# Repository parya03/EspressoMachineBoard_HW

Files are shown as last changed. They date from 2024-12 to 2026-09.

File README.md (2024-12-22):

Espresso Machine Board Project
Make a new controller for my Chefman CraftBrew

TODO Documentation

Power converter KiCad symbol and footprint from:
https://github.com/yaserharba/WX-DC12003_Kicad

Reverse Engineering notes for now:

Single shot brew temp: ~180 F
Steam temp: ~205 F at valve, ~230F at boiler
NTC 100k(?) Thermistor
- ~114kOhm at ~22.5C
CMS79FT738 MCU
13 x 6 cm board
3/16” OD, 1/8”(?) ID tubing

Why is OPV before boiler? Where to put actual pressure sensor?

Label says 1350W power consumption, 120VAC 60Hz

Board mounting screw:
30-23.5‎ = 6.5 from edge of hole to edge of hole
Right side hole positioned at 3.5cm from top, 2.5mm from right side of board (to middle of hole)

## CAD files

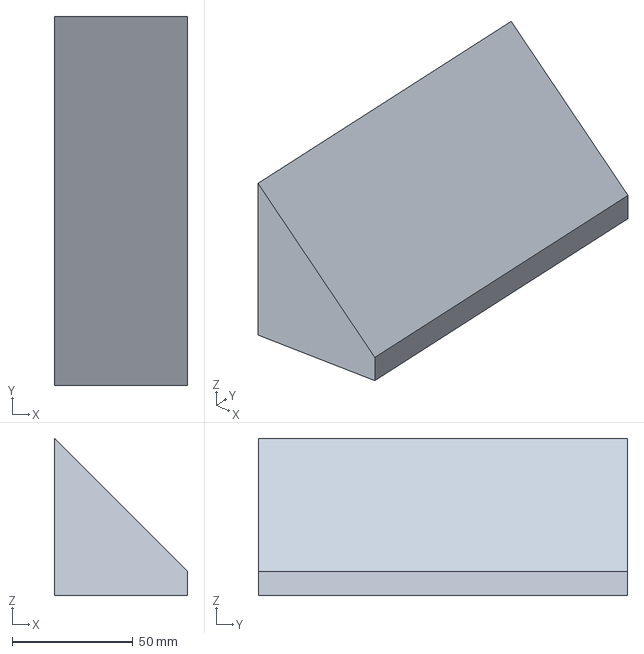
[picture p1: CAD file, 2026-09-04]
3DPrint/EspressoMachineBoardEnclosure.FCStd
55.2 x 153.0 x 65.2 mm

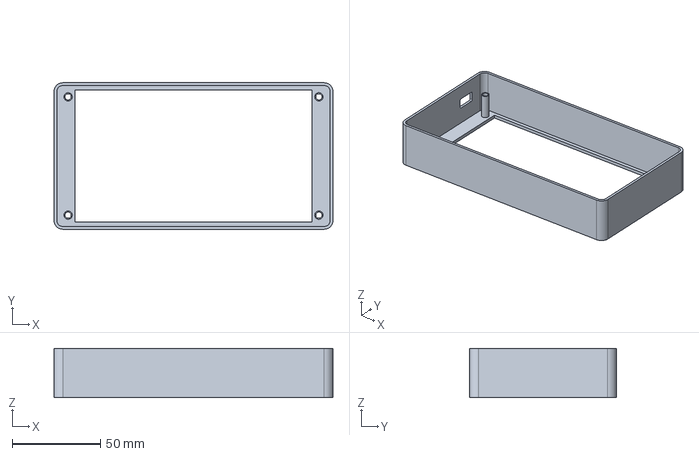
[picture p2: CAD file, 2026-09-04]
3DPrintSmall/CoffeeMachineSmallEnclosure.FCStd
158.0 x 83.0 x 28.0 mm

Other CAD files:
3DPrintSmall/CoffeeMachineSmallEnclosure-Body.3mf

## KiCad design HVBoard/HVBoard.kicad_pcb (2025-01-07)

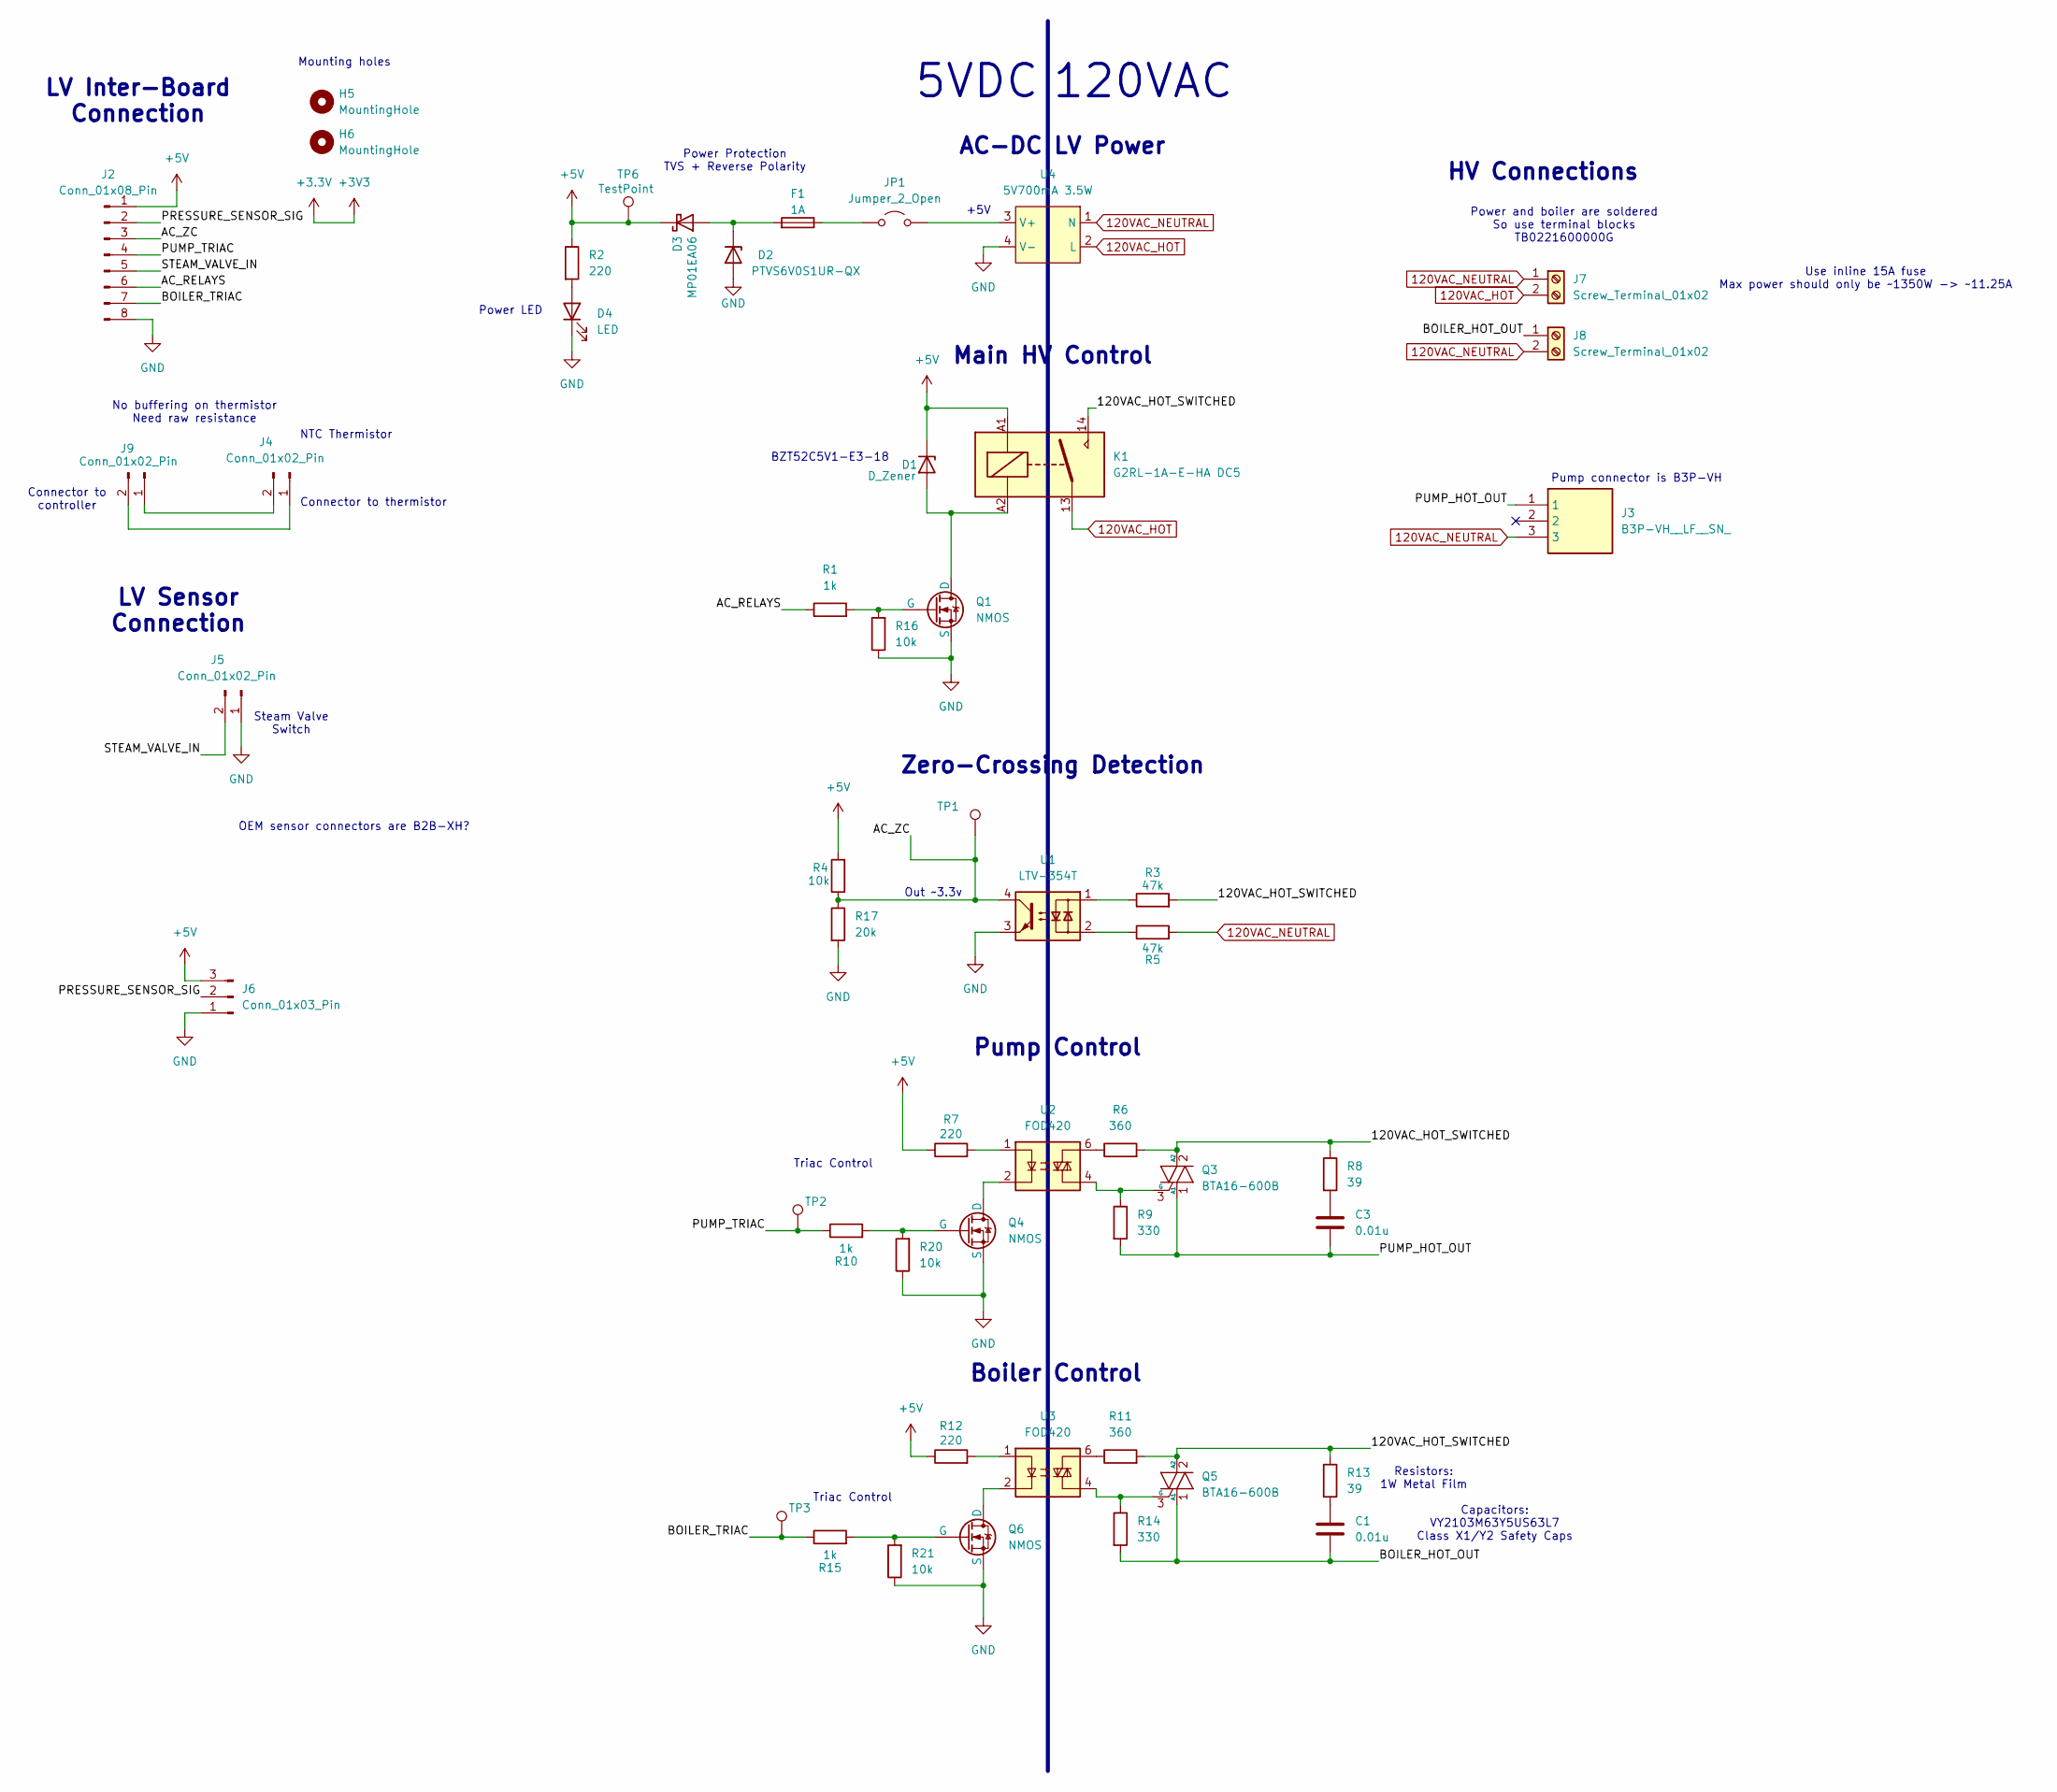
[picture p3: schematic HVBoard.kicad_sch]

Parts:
C1, C3: 0.01u; C_Disc_D11.0mm_W5.0mm_P7.50mm
D1: D_Zener; D_SOD-123
D2: PTVS6V0S1UR-QX; Nexperia_CFP3_SOD-123W
D3: MP01EA06; D_SOD-123
D4: LED; LED_0603_1608Metric; Mouser # 755-SMLD12EN1WT86
F1: 1A; Fuse_0603_1608Metric_Pad1.05x0.95mm_HandSolder
H5, H6: MountingHole; MountingHole_3.2mm_M3
J2: Conn_01x08_Pin; JST_PH_B8B-PH-K_1x08_P2.00mm_Vertical
J3: B3P-VH__LF__SN_; HDRV3W114P0X396_1X3_1182X850X1090P; Manufacturer_Part_Number B3P-VH (LF)(SN)
J4, J5, J9: Conn_01x02_Pin; JST_XH_B2B-XH-AM_1x02_P2.50mm_Vertical
J6: Conn_01x03_Pin; JST_XH_B3B-XH-AM_1x03_P2.50mm_Vertical
J7, J8: Screw_Terminal_01x02; TerminalBlock_bornier-2_P5.08mm
JP1: Jumper_2_Open; SolderJumper-2_P1.3mm_Open_Pad1.0x1.5mm
K1: G2RL-1A-E-HA DC5; Relay_SPST_Omron_G2RL-1A-E
Q1, Q4, Q6: NMOS; SOT-23
Q3, Q5: BTA16-600B; TO-220-3_Vertical
R1, R10, R15: 1k; R_0603_1608Metric_Pad0.98x0.95mm_HandSolder
R2: 220; R_0603_1608Metric; Mouser # 71-CRCW0603-665-E3
R3, R5: 47k; R_1206_3216Metric_Pad1.30x1.75mm_HandSolder
R4, R16, R20, R21: 10k; R_0603_1608Metric_Pad0.98x0.95mm_HandSolder
R6, R11: 360; R_1206_3216Metric_Pad1.30x1.75mm_HandSolder
R7, R12: 220; R_0603_1608Metric_Pad0.98x0.95mm_HandSolder
R8, R13: 39; R_Axial_DIN0207_L6.3mm_D2.5mm_P10.16mm_Horizontal
R9, R14: 330; R_1206_3216Metric_Pad1.30x1.75mm_HandSolder
R17: 20k; R_0603_1608Metric_Pad0.98x0.95mm_HandSolder
TP1, TP2, TP3, TP6: TestPoint; PinHeader_1x01_P2.54mm_Vertical
U1: LTV-354T; SO-4_4.4x3.6mm_P2.54mm
U2, U3: FOD420; DIP-6_W7.62mm
U4: 5V700mA 3.5W; WX-DC12003

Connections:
120VAC_HOT: J7.2, K1.13, U4.2 (L)
120VAC_NEUTRAL: J3.3, J7.1, J8.2, R5.2, U4.1 (N)
+5V: D1.1 (K), D3.1 (K), J2.1, J6.3, K1.A1, R2.1, R4.2, R7.1, R12.1, TP6.1
/120VAC_HOT_SWITCHED: K1.14, Q3.2 (A2), Q5.2 (A2), R3.2, R6.2, R8.1, R11.2, R13.1
/AC_RELAYS: J2.6, R1.1
/AC_ZC: J2.3, R4.1, R17.1, TP1.1, U1.4
/BOILER_HOT_OUT: C1.2, J8.1, Q5.1 (A1), R14.2
/BOILER_TRIAC: J2.7, R15.1, TP3.1
/PRESSURE_SENSOR_SIG: J2.2, J6.2
/PUMP_HOT_OUT: C3.2, J3.1, Q3.1 (A1), R9.2
/PUMP_TRIAC: J2.4, R10.1, TP2.1
/STEAM_VALVE_IN: J2.5, J5.2
GND: D2.2 (A), D4.1 (K), J2.8, J5.1, J6.1, Q1.3 (S), Q4.3 (S), Q6.3 (S), R16.1, R17.2, R20.1, R21.1, U1.3, U4.4 (V-)
unnamed: C1.1, R13.2
unnamed: C3.1, R8.2
unnamed: D1.2 (A), K1.A2, Q1.1 (D)
unnamed: D2.1 (K), D3.2 (A), F1.2
unnamed: D4.2 (A), R2.2
unnamed: J4.1, J9.2
unnamed: J4.2, J9.1
unnamed: JP1.1 (A), U4.3 (V+)
unnamed: F1.1, JP1.2 (B)
unnamed: Q1.2 (G), R1.2, R16.2
unnamed: Q3.3 (G), R9.1, U2.4
unnamed: Q4.1 (D), U2.2
unnamed: Q4.2 (G), R10.2, R20.2
unnamed: Q5.3 (G), R14.1, U3.4
unnamed: Q6.1 (D), U3.2
unnamed: Q6.2 (G), R15.2, R21.2
unnamed: R3.1, U1.1
unnamed: R5.1, U1.2
unnamed: R6.1, U2.6
unnamed: R7.2, U2.1
unnamed: R11.1, U3.6
unnamed: R12.2, U3.1

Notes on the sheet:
Connector to thermistor
Zero-Crossing Detection
Triac Control
Connector to controller
Mounting holes
Power and boiler are soldered So use terminal blocks TB0221600000G
+5V
Out ~3.3v
Power LED
Pump Control
OEM sensor connectors are B2B-XH?
Steam Valve Switch
5VDC
LV Inter-Board Connection
NTC Thermistor
Use inline 15A fuse Max power should only be ~1350W -> ~11.25A
BZT52C5V1-E3-18
AC-DC LV Power
Boiler Control
Pump connector is B3P-VH
No buffering on thermistor Need raw resistance
HV Connections
LV Sensor Connection
Main HV Control
Capacitors: VY2103M63Y5US63L7 Class X1/Y2 Safety Caps
Power Protection TVS + Reverse Polarity
Resistors: 1W Metal Film
120VAC

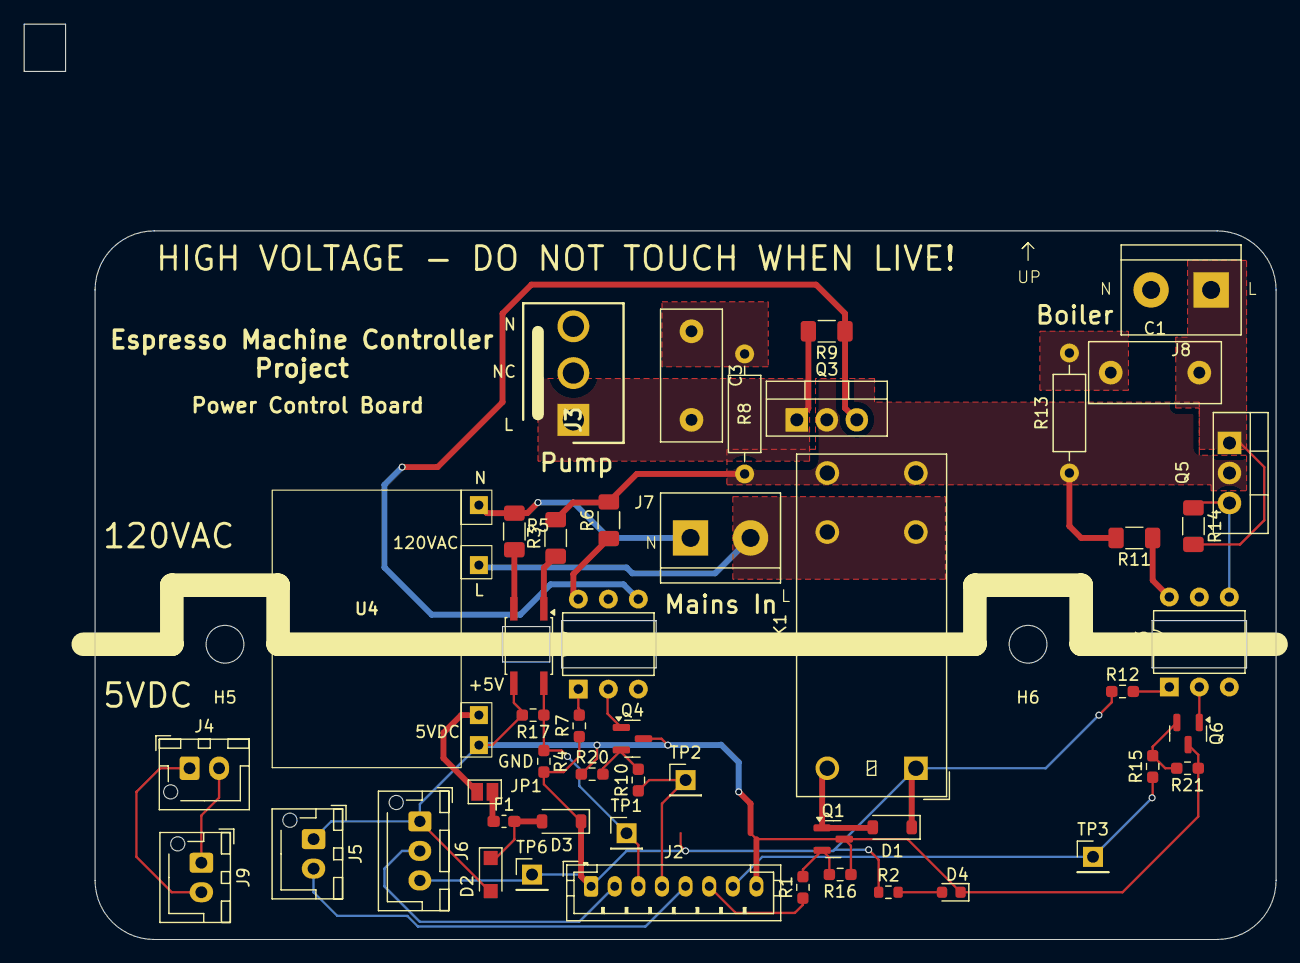
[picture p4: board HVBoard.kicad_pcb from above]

Board: 2 copper layers, 100.0 x 60.0 mm, 51 parts (0 on the bottom side), 35 nets.

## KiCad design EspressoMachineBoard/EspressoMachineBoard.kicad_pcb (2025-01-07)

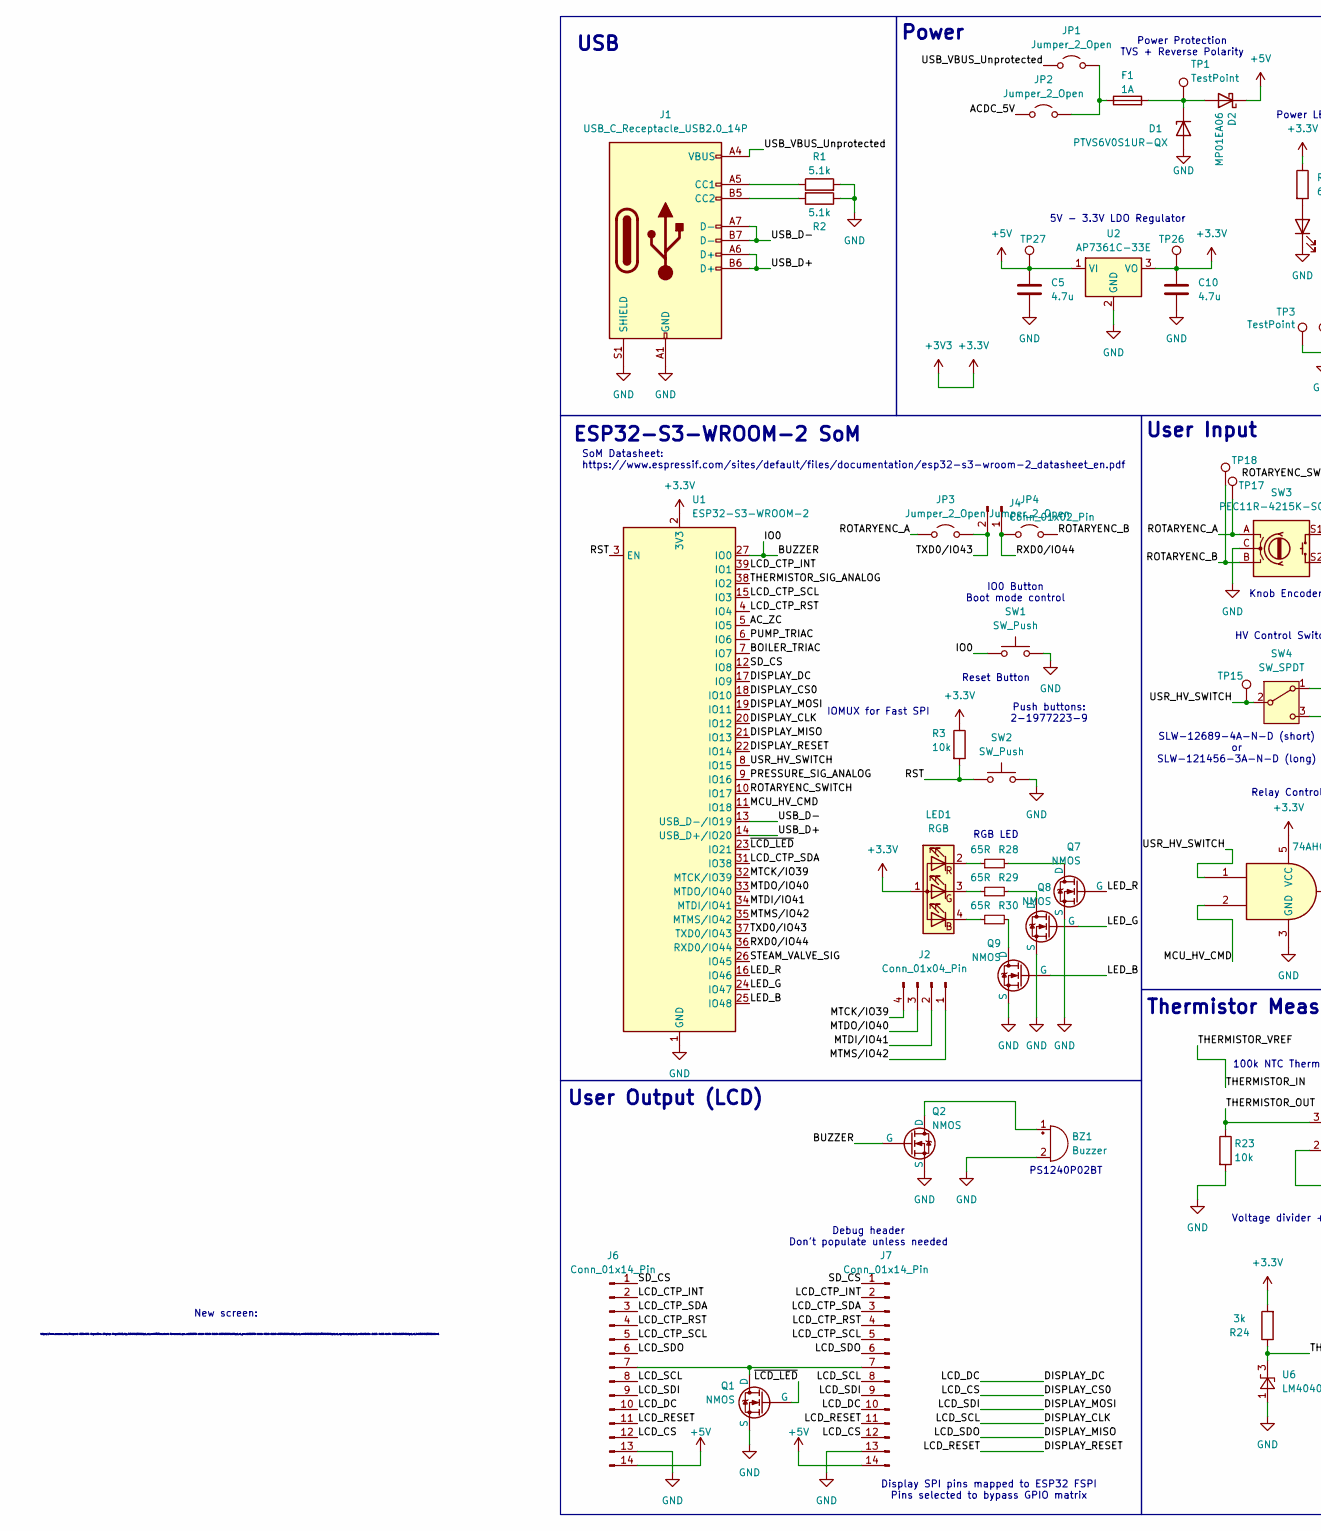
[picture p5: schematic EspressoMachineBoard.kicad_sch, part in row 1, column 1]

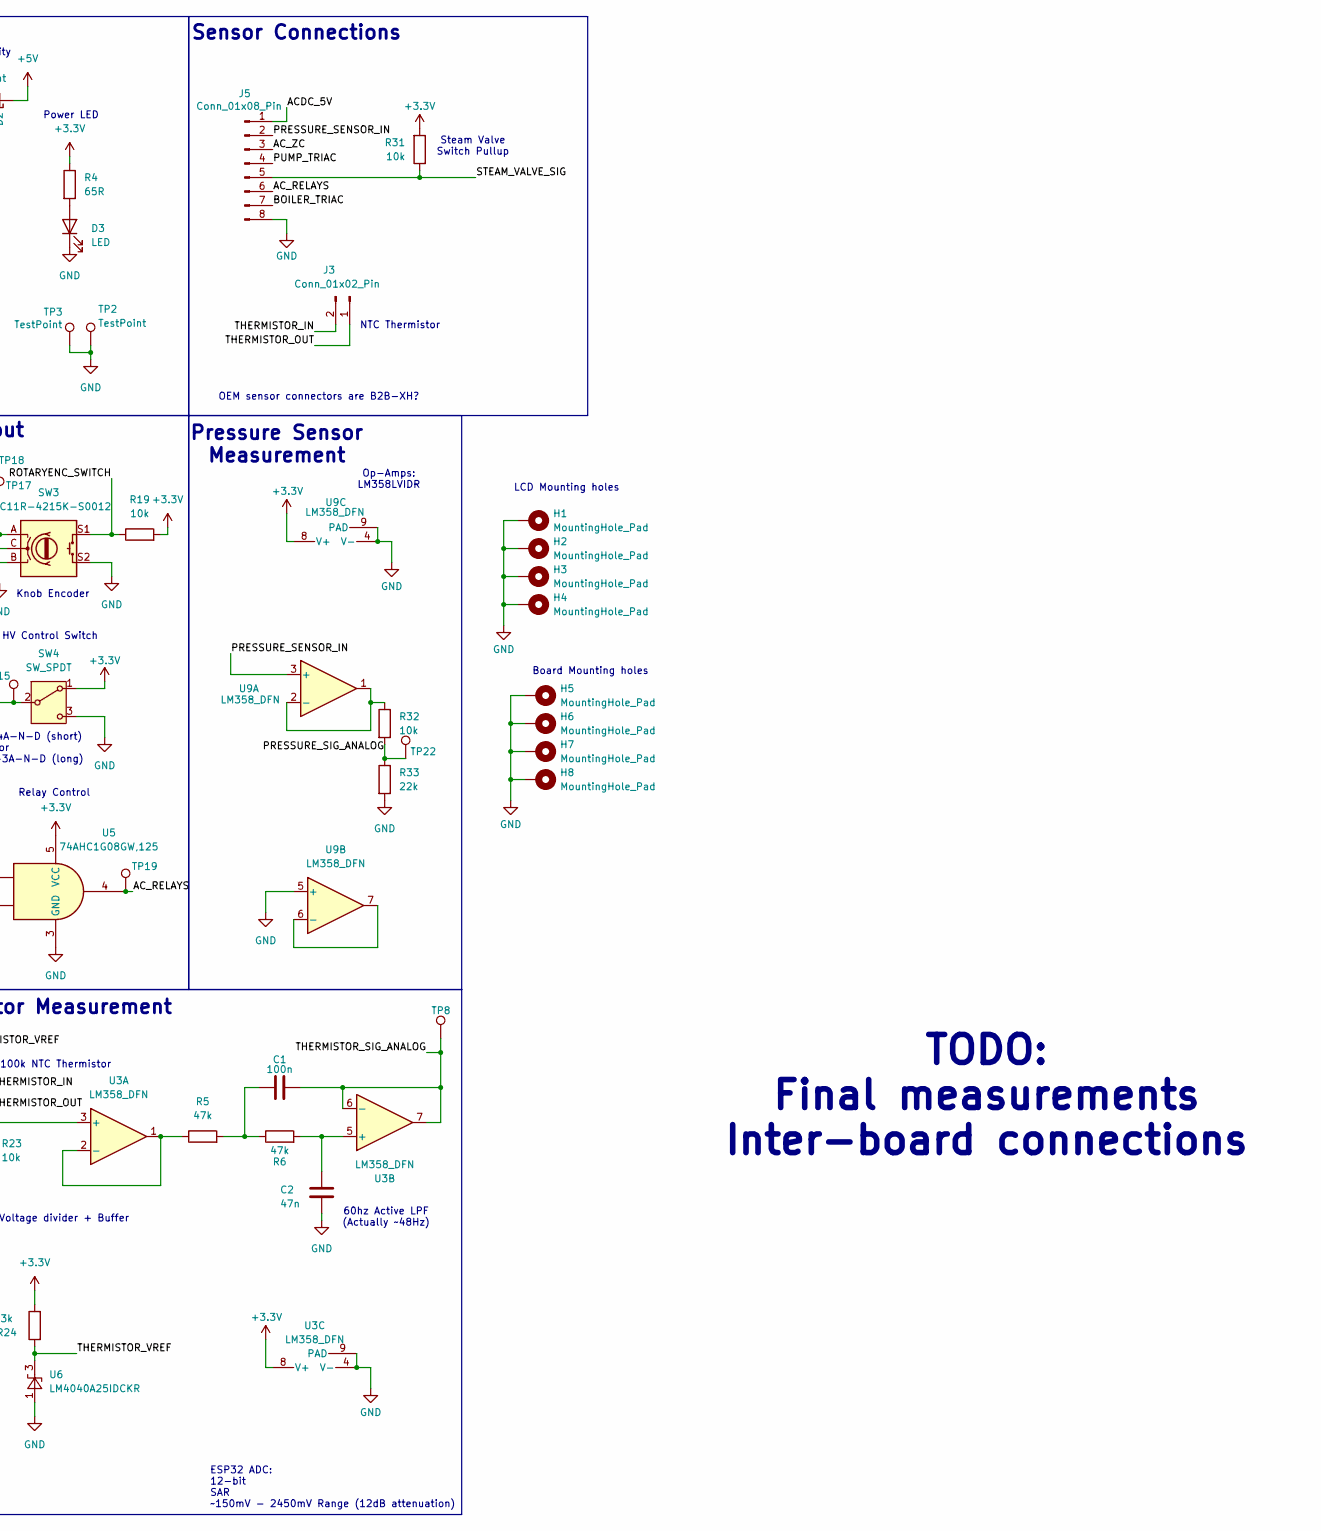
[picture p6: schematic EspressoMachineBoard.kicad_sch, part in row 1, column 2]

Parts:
BZ1: Buzzer; Buzzer_TDK_PS1240P02BT_D12.2mm_H6.5mm
C1: 100n; C_0603_1608Metric_Pad1.08x0.95mm_HandSolder
C2: 47n; C_0603_1608Metric_Pad1.08x0.95mm_HandSolder
C5, C10: 4.7u; C_0603_1608Metric; Mouser # 81-GCJ188C70J475KE2D
D1: PTVS6V0S1UR-QX; Nexperia_CFP3_SOD-123W
D2: MP01EA06; D_SOD-123
D3: LED; LED_0603_1608Metric; Mouser # 755-SMLD12EN1WT86
F1: 1A; Fuse_0603_1608Metric_Pad1.05x0.95mm_HandSolder
H1, H2, H3, H4: MountingHole_Pad; MountingHole_3.2mm_M3_DIN965
H5, H6, H7, H8: MountingHole_Pad; MountingHole_3.2mm_M3_DIN965_Pad
J1: USB_C_Receptacle_USB2.0_14P; USB_C_Receptacle_GCT_USB4110
J2: Conn_01x04_Pin; PinSocket_1x04_P2.54mm_Vertical
J3: Conn_01x02_Pin; JST_XH_B2B-XH-AM_1x02_P2.50mm_Vertical
J4: Conn_01x02_Pin; PinSocket_1x02_P2.54mm_Vertical
J5: Conn_01x08_Pin; JST_PH_B8B-PH-K_1x08_P2.00mm_Vertical
J6, J7: Conn_01x14_Pin; PinSocket_1x14_P2.54mm_Vertical
JP1, JP2, JP3, JP4: Jumper_2_Open; SolderJumper-2_P1.3mm_Open_Pad1.0x1.5mm
LED1: RGB; LED_Cree-PLCC4_3.2x2.8mm_CCW; Mouser # 941-CLV1LFKBCJ1N1E1B
Q1, Q2, Q7, Q8, Q9: NMOS; SOT-23
R1, R2: 5.1k; R_0603_1608Metric_Pad0.98x0.95mm_HandSolder
R3, R19, R23, R31, R32: 10k; R_0603_1608Metric_Pad0.98x0.95mm_HandSolder
R4: 65R; R_0603_1608Metric; Mouser # 71-CRCW0603-665-E3
R5, R6: 47k; R_0603_1608Metric_Pad0.98x0.95mm_HandSolder
R24: 3k; R_0603_1608Metric_Pad0.98x0.95mm_HandSolder
R28, R29, R30: 65R; R_0603_1608Metric_Pad0.98x0.95mm_HandSolder
R33: 22k; R_0603_1608Metric_Pad0.98x0.95mm_HandSolder
SW1, SW2: SW_Push; SW_Push_1P1T_NO_6x6mm_H9.5mm
SW3: PEC11R-4215K-S0012; RotaryEncoder_Alps_EC11E-Switch_Vertical_H20mm
SW4: SW_SPDT; SW_Slide_SPDT_Straight_CK_OS102011MS2Q
TP1, TP2, TP3, TP8, TP15, TP17, TP18, TP19, TP22, TP26, TP27: TestPoint; PinHeader_1x01_P2.54mm_Vertical
U1: ESP32-S3-WROOM-2
U2: AP7361C-33E; SOT-223-3_TabPin2; Mouser # 621-AP7361C-33E-13
U3, U9: LM358_DFN; SOIC-8_3.9x4.9mm_P1.27mm
U5: 74AHC1G08GW,125; SOT-353_SC-70-5_Handsoldering
U6: LM4040A25IDCKR; SOT-353_SC-70-5

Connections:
+3.3V: C10.1, LED1.1 (A), R3.1, R4.1, R19.2, R24.2, R31.2, SW4.1 (A), TP26.1, U1.2 (3V3), U2.3 (VO), U3.8 (V+), U5.5 (VCC), U9.8 (V+)
+5V: C5.1, D2.1 (K), J6.14, J7.14, TP27.1, U2.1 (VI)
/ACDC_5V: J5.1, JP2.1 (A)
/AC_RELAYS: J5.6, TP19.1, U5.4
/AC_ZC: J5.3, U1.5 (IO5)
/BOILER_TRIAC: J5.7, U1.7 (IO7)
/BUZZER: Q2.2 (G), SW1.1, U1.27 (IO0)
/DISPLAY_CLK: J6.8, J7.8, U1.20 (IO12)
/DISPLAY_CS0: J6.12, J7.12, U1.18 (IO10)
/DISPLAY_DC: J6.10, J7.10, U1.17 (IO9)
/DISPLAY_MISO: J6.6, J7.6, U1.21 (IO13)
/DISPLAY_MOSI: J6.9, J7.9, U1.19 (IO11)
/DISPLAY_RESET: J6.11, J7.11, U1.22 (IO14)
/LCD_CTP_INT: J6.2, J7.2, U1.39 (IO1)
/LCD_CTP_RST: J6.4, J7.4, U1.4 (IO4)
/LCD_CTP_SCL: J6.5, J7.5, U1.15 (IO3)
/LCD_CTP_SDA: J6.3, J7.3, U1.31 (IO38)
/LED_B: Q9.2 (G), U1.25 (IO48)
/LED_G: Q8.2 (G), U1.24 (IO47)
/LED_R: Q7.2 (G), U1.16 (IO46)
/MCU_HV_CMD: U1.11 (IO18), U5.2
/MTCK/IO39: J2.4, U1.32 (MTCK/IO39)
/MTDI/IO41: J2.2, U1.34 (MTDI/IO41)
/MTDO/IO40: J2.3, U1.33 (MTDO/IO40)
/MTMS/IO42: J2.1, U1.35 (MTMS/IO42)
/PRESSURE_SENSOR_IN: J5.2, U9.3 (+)
/PRESSURE_SIG_ANALOG: R32.2, R33.1, TP22.1, U1.9 (IO16)
/PUMP_TRIAC: J5.4, U1.6 (IO6)
/ROTARYENC_A: JP3.1 (A), SW3.A, TP17.1
/ROTARYENC_B: JP4.2 (B), SW3.B, TP18.1
/ROTARYENC_SWITCH: R19.1, SW3.S1, U1.10 (IO17); also elsewhere on the board
/RST: R3.2, SW2.1, U1.3 (EN)
/RXD0/IO44: J4.1, JP4.1 (A), U1.36 (RXD0/IO44)
/SD_CS: J6.1, J7.1, U1.12 (IO8)
/STEAM_VALVE_SIG: J5.5, R31.1, U1.26 (IO45)
/THERMISTOR_IN: J3.2, R24.1, U6.3 (K)
/THERMISTOR_OUT: J3.1, R23.1, U3.3 (+)
/THERMISTOR_SIG_ANALOG: C1.1, TP8.1, U1.38 (IO2), U3.6 (-), U3.7
/TXD0/IO43: J4.2, JP3.2 (B), U1.37 (TXD0/IO43)
/USB_D+: J1.A6 (D+), J1.B6 (D+), U1.14 (USB_D+/IO20)
/USB_D-: J1.A7 (D-), J1.B7 (D-), U1.13 (USB_D-/IO19)
/USB_VBUS_Unprotected: J1.A4 (VBUS), J1.A9 (VBUS), J1.B4 (VBUS), J1.B9 (VBUS), JP1.1 (A)
/USR_HV_SWITCH: SW4.2 (B), TP15.1, U1.8 (IO15), U5.1
/~LCD_LED: Q1.2 (G), U1.23 (IO21)
GND: BZ1.2 (-), C2.2, C5.2, C10.2, D1.2 (A), D3.1 (K), H1.1, H2.1, H3.1, H4.1, H5.1, H6.1, H7.1, H8.1, J1.A1 (GND), J1.A12 (GND), J1.B1 (GND), J1.B12 (GND), J1.S1 (SHIELD), J5.8, J6.13, J7.13, Q1.3 (S), Q2.3 (S), Q7.3 (S), Q8.3 (S), Q9.3 (S), R1.2, R2.1, R23.2, R33.2, SW1.2, SW2.2, SW3.C, SW3.S2, SW4.3 (C), TP2.1, TP3.1, U1.1 (GND), U1.40 (GND), U1.41 (GND), U2.2 (GND), U3.4 (V-), U3.9 (PAD), U5.3 (GND), U6.1 (A), U9.4 (V-), U9.5 (+), U9.9 (PAD)
unnamed: BZ1.1 (+), Q2.1 (D)
unnamed: C1.2, R5.2, R6.1
unnamed: D1.1 (K), D2.2 (A), F1.2, TP1.1
unnamed: D3.2 (A), R4.2
unnamed: J1.A5 (CC1), R1.1
unnamed: J1.B5 (CC2), R2.2
unnamed: J6.7, J7.7, Q1.1 (D)
unnamed: F1.1, JP1.2 (B), JP2.2 (B)
unnamed: LED1.4 (BK), R30.1
unnamed: LED1.3 (GK), R29.1
unnamed: LED1.2 (RK), R28.1
unnamed: Q7.1 (D), R28.2
unnamed: Q8.1 (D), R29.2
unnamed: Q9.1 (D), R30.2
unnamed: R5.1, U3.1, U3.2 (-)
unnamed: C2.1, R6.2, U3.5 (+)
unnamed: R32.1, U9.1, U9.2 (-)
unnamed: U9.6 (-), U9.7

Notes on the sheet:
60hz Active LPF (Actually ~48Hz)
Thermistor Measurement
Debug header Don't populate unless needed
ESP32 ADC: 12-bit SAR ~150mV - 2450mV Range (12dB attenuation)
SLW-12689-4A-N-D (short) or SLW-121456-3A-N-D (long)
OEM sensor connectors are B2B-XH?
Steam Valve Switch Pullup
Push buttons: 2-1977223-9
Relay Control
100k NTC Thermistor
User Input
Board Mounting holes
New screen:
IOMUX for Fast SPI
Power LED
Power Protection TVS + Reverse Polarity
5V - 3.3V LDO Regulator
SoM Datasheet: https://www.espressif.com/sites/default/files/documentation/esp32-s3-wroom-2_datasheet_en.pdf
Pressure Sensor Measurement
TODO: Final measurements Inter-board connections
Reset Button
Voltage divider + Buffer
User Output (LCD)
USB
RGB LED
ESP32-S3-WROOM-2 SoM
LCD Mounting holes
Sensor Connections
HV Control Switch
Knob Encoder
PS1240P02BT
Power
https://www.amazon.com/Hosyond-320x480-Capacitive-Display-Mega2560/dp/B0CRGQN58D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…
Display SPI pins mapped to ESP32 FSPI Pins selected to bypass GPIO matrix
Op-Amps: LM358LVIDR
IO0 Button Boot mode control
NTC Thermistor

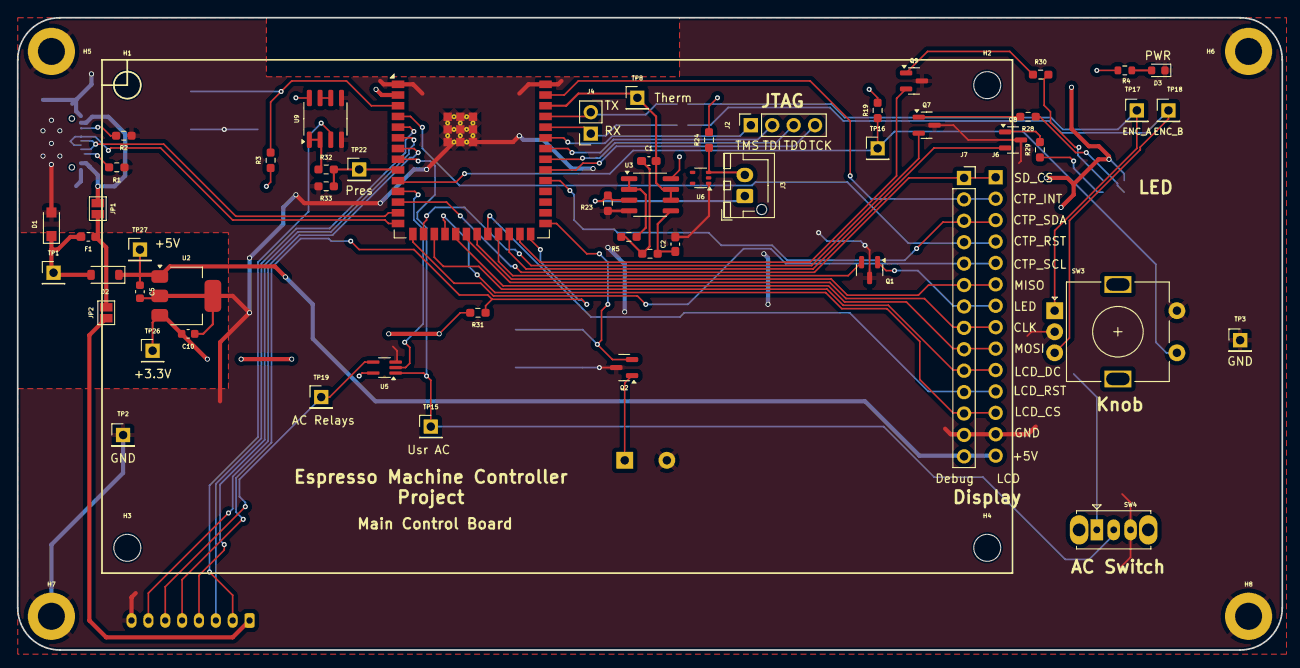
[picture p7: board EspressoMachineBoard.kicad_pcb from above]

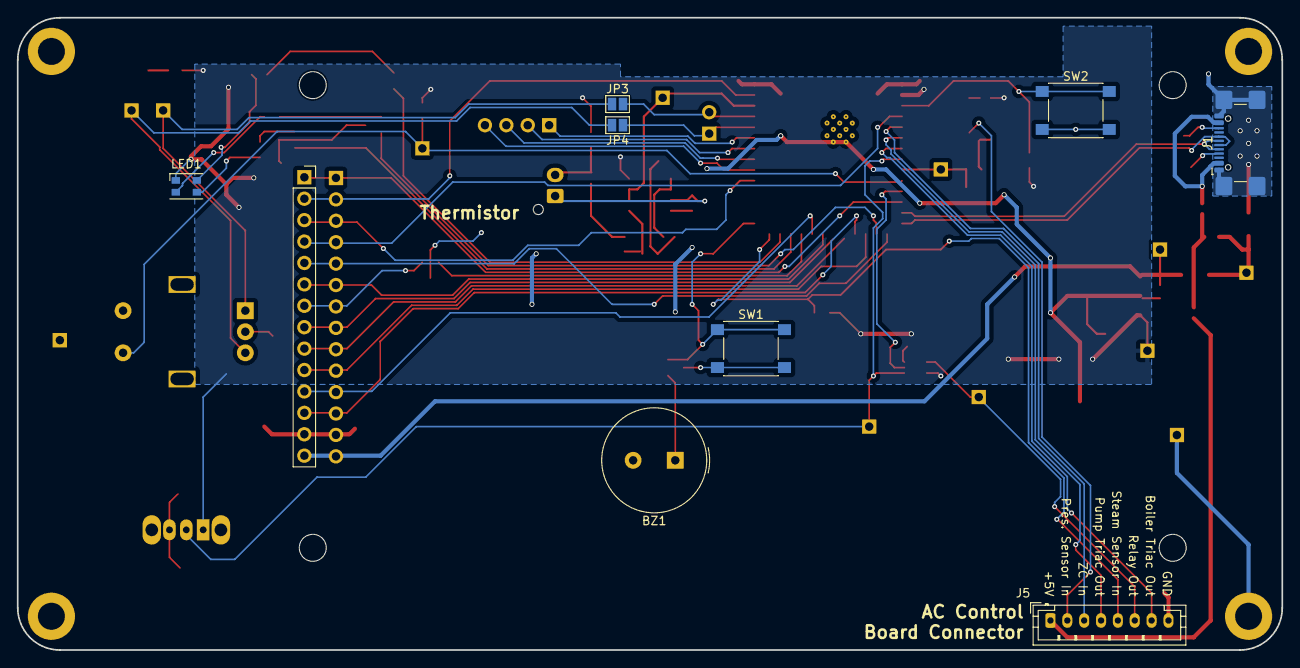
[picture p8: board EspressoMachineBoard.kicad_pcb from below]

Board: 2 copper layers, 150.0 x 75.0 mm, 71 parts (9 on the bottom side), 63 nets.

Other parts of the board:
TP16: TestPoint; PinHeader_1x01_P2.54mm_Vertical

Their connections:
/ROTARYENC_SWITCH: TP16.1; also elsewhere on the board

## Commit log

2024-12-19 Schematic initial commit
    [EspressoMachineBoard.kicad_pcb, EspressoMachineBoard.kicad_sch]
2024-12-20 Almost done with schematic
    [EspressoMachineBoard.kicad_sch]
2024-12-20 Split into 2 board
    [EspressoMachineBoard.kicad_pcb, EspressoMachineBoard.kicad_sch, HVBoard.kicad_pcb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]
2024-12-22 More work
    [EspressoMachineBoard.kicad_sch, HVBoard.kicad_pcb, HVBoard.kicad_sch]
2024-12-25 More HV work
    [HVBoard.kicad_pcb, HVBoard.kicad_sch]
2025-01-04 Reddit feedback integrated into HV board
    [HVBoard.kicad_pcb, HVBoard.kicad_sch]
2025-01-07 Boards finalized and ordered
    [EspressoMachineBoard.kicad_pcb, EspressoMachineBoard.kicad_sch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]
2025-02-12 Added issues
    [EspressoMachineBoard.kicad_sch]
2025-11-11 Enclosure model started
    [EspressoMachineBoardEnclosure.FCStd]
